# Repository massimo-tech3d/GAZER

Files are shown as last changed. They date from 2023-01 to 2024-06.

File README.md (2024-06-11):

# GAZER

it's a no-hassles, sensors based, GOTO system to drive amateurial telescopes on altazimutal mounts.

No-hassles means that you setup the scope, launch the automatic calibration procedure, acquire the GPS position on your smartphone, and you are ready to aim at your desired sky objects. **No star alignement required**. **No internet connection is required**, thus it can be used in remote, dark sky location, where data services may be unavailbale.

The telescope aim is determined via magnetometer and accelerometer sensors, while corrections/precise centering are commanded manually via a Joystick.

Note that the precision of sensors, especially magnetometers, is limited to half a degree. While this is not sufficient for precision tracking, it is well enough to hit the targeted object in the field of view of a low power eyepiece.

Object Tracking is then based on precise calculations, not on the sensors readings.

The system is composed of the following components:
* Sensors for azimuth and altitude determination. These are rigidly fixed to the telscope tube or mount.
* Arduino microcontroller (Teensy 4.0 is required) which performs
	* Magnetometer calibration
	* Sensors readings
	* Calculation of Altitude and Azimuth
	* Joystick movement readouts
* a PCB to be populated with Teensy and Stepper Drivers and to plug-in sensors and joystick cables. The PCB is finally plugged in the RPi GPIO connector.
* Raspberry Pi 3 hosts the Elixir/Nerves code to
	*  control the stepper motors
	*  read the data acquired by the Teensy microcontroller
	*  execute the astronomical algorithms for aiming and tracking objects
	*  connect to the user's smartphone to acquire GPS position
	*  provides the access point to connect the smartphone to access the **Web Based GUI** for scope control.
	*  provides a full blown version of the NGC/IC catalogues and solar system object positions
* User's Smartphone
	* The user needs to install the "GPSd Forwarder" app -- opensource and available on Google Play Store -- therefore only Android phones are currently supported, however a flutter app is in the plans which will support both Android and IOS devices. No schedule available at the moment.
	* Any mobile web browser to display the GUI

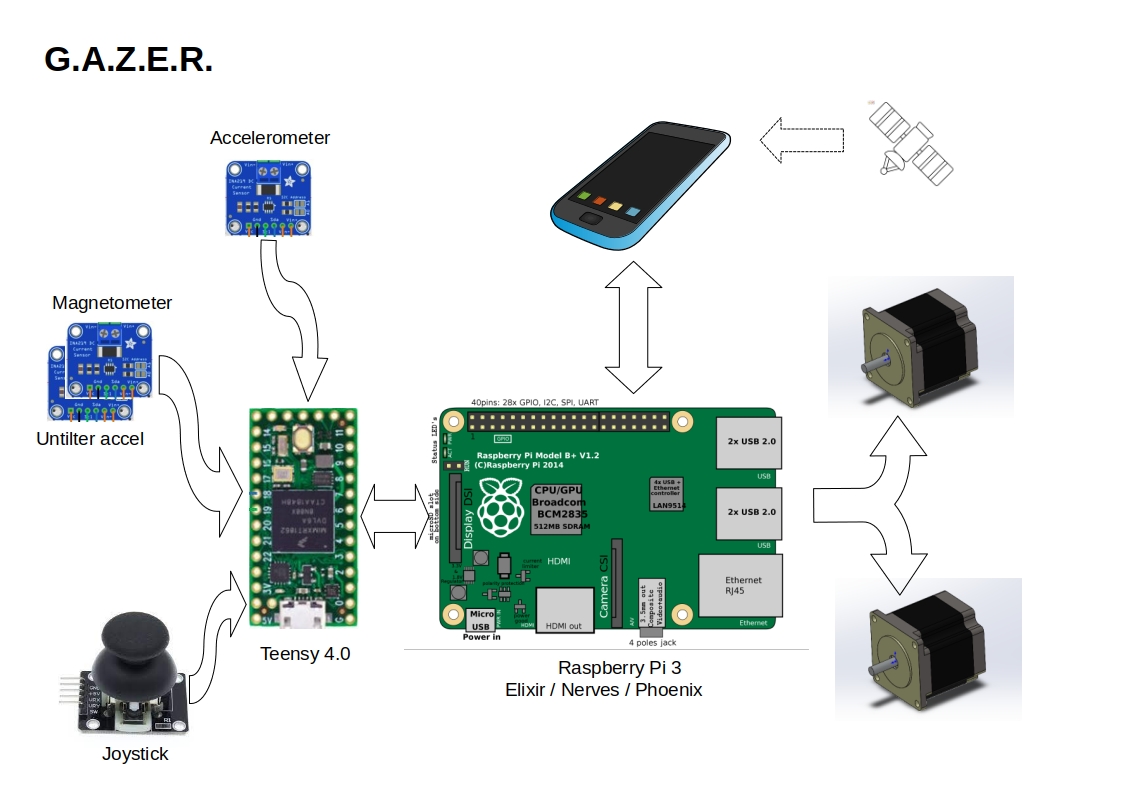
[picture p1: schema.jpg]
gazer block diagram

More information on each component is provided in the respective folders.

## What's still to be completed - work in progress

- [ ] Unit tests
- [ ] Documentation
- [ ] Flutter application as alternative to browser based GUI

## How to build
1. download gerber files from the hardware sections and get the pcb etched by your favorite service
2. follow the instructions in hardware folder
3. flash the teensy with the sketch in arduino folder
4. plug the teensy on the PCB socket
5. plug the PCB onto the RPi3 GPIO
6. flash the RPi3 card with the nerves image provided in raspberry folder. Or, if preferred, compile the source code and use the elixir/nerves commands to flash the card
7. connect sensors and motors to the RPi box
8. boot the RPi3
9. Verify the smartphone connectivity. Select gazer access point and connect to 192.168.3.1
10. install "GPSd Forwarder" from Play Store and turn it on
11. Enjoy mant star gazing nights !

## License
the project is released under AGPLv3 License (the dependencies have their own licences)

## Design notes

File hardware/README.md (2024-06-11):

## Hardware description
The Hardware for GAZER system is composed of following items:
* 1 x Raspberry Pi 3
* 1 x Teensy 4.0
* 1 x PCB - Gerber files available in this repository
* 2 x Stepper motor controller. Tested with DRV8825. Any other model with same pinout, and capable of 32 µsteps per step, should be ok
* 1 x Analogue Joystick with 5 pins connector, 2 axis 1 button
* 2 x 4 pins cables and connectors for the sensors
* 1 x 5 pins cable and connectors for the joystick
* 1 x MEMS Magnetometer. Suppeorted: LIS3MDL and PNI RM3100
* 1 x MEMS Accelerometer as untilter. Supported: MMA8451 and MPU6050
* 1 x MEMS Accelerometer for Attitude. Supported LSM6DSV

### PCB Assembly
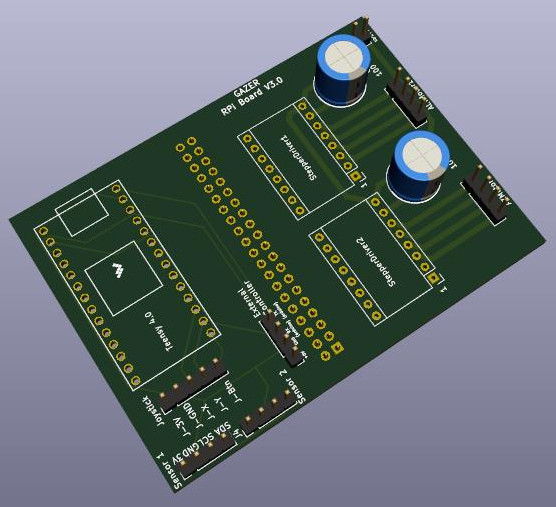
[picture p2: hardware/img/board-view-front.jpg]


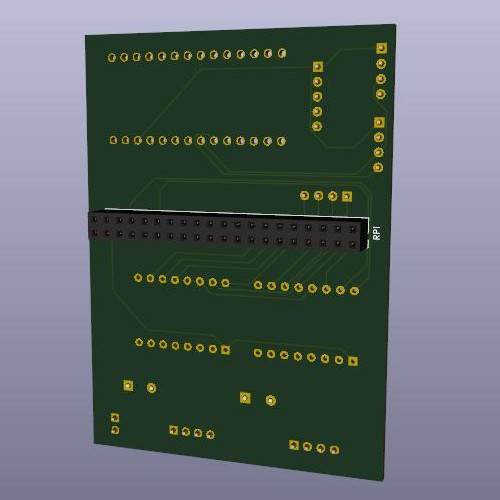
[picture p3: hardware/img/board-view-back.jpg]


The PCB shows clear indications about what needs to be plugged where. Just solder the two 100uF capacitors (beware of polarity), the sockets and pin connectors where they need to be and plug in the components.

**Note**
The 40 pin socket to the Raspberry PI needs to be positioned on the back of the PCB (solder on the front).

The two sensors sockets are interchangeable, sensors block and accelerometer can be plugged in either one.

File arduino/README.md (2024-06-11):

The repository includes two sketches, Gazza2D and Gazza3D.

Their role is to read the sensors and calculate Altitude and Azimuth of the Telescope OTA for the main Gazer app, which run on the connected Raspberry Pi 3.

The sensors required are an accelerometer (rotating with the OTA) to calculate the Altidude, and a Magnetometer to calculate the Azimuth.

The difference between the two sketches is how the magnetometer is handled.

# 2D
The 2D Sketch requires the magnetometer to be positioned flat on the mount and rotate with it, disregarding the OTA inclinations. It uses a second accelerometer on the same board of the magnetometer to compensate for potential off levels - tripod and mount or a mismounted magnetometer board, **Small degrees off level (say up to 5° or 10° at best) can be compensated by the second accelerometer**

The second accelerometer is strongly reccommended but the system will work also without it. In this case you should ensure that the telescope mount and the magnetometer itself are perfectly level, or the Azimuth readings will be way off.

The sensor calibration carousels 360° back and forth the azimuth axis, with the OTA conveniently positioned verticallly, and then performs 2D ellipse fitting of the sensors readings to calculate hard iron and soft iron correction parameters.

The carouselling requires approximately 4 minutes.

# 3D
The 3D Sketch requires magnetometer and accelerometer on the same board on the OTA rotating with the OTA both in Azimuth and Altitude. The second accelerometer in not required.

The sensor calibration carousels 360° back and forth two times the azimuth axis, with the OTA positioned at 0° (horizontal), 45°, 90° and 135° (backtilted), and then performs 3D ellipsoid fitting of the sensors readings to calculate hard iron and soft iron correction parameters.

The carouselling requires approximately 10 minutes.

## Which should be chosen
It depends on you mount and setup. For dobsons you should chose the 2D version, since it does not backtilt the OTA and because there will not be problems in finding a good place to install the magnetomer board, away at least 20cm from motors, The aluminium/wooden OTA will not cause interferences.

It also takes less time to calibrate.

Telescopes mounted on other types of platform can also use the 2D skecth, if you can position the magnetometer away from motors and away from the OTA (if this is made of ferromagnetic metal).

If this is not the case, it is necessary to use the 3D version and hook the sensors on the OTA (if not ferromagnetic) or in a spot on the mount that follows the OTA movements.

In case of 2D version and magnetometer too close to metallic OTA, this will disturb the magnetic field when changing it's altitude. There is a compensation function to limit this phenomenon but it is reccommended to avoid it at all, rather than compensating it.

In synthesis the main advantages of the two setups are:
* 2D version
	- faster calibration procedure
	- OTA vertical during carouselling - no issues with space requirements
	- does not backtilt the OTA during calibration
* 3D version
	- less number of sensors
	- just one sensor board and one sensor cable

In both sketches the magnetometer calibration procedure is intiated by the user and coordinated by the Elixir software on the Raspberry.

The Accelerometer calibration is much simpler, the OTA is placed horizontal and a reading is taken via a button on the phone GUI. The same is then repeatd with the OTA in vertical position.

# Hardware parts

## Microcontroller
The magnetometer calibration and untilting require extensive float operations. Therefore the AVR Microcontrollers are not suitable. The reccommended choice is a Teensy 4.0 board.

We have briefly tested the skecth also on an ESP32 WROOM board and it compiles and runs, however we have not done any extensive testing. We preferred the Teensy over the ESP32 because of its smaller footprint.

The sketch, and the PCB, only support the Teensy 4.0. Support for the ESP, as well as other same level micros, would require changing the pinout mappings in the sketch and changing the PCB design.

## Supported MEMS are:
3D version:
* Magnetometers: ST LIS3MDL (reccommended), PNI RM3100
* Accelerometer: ST LSM6DSV (reccommended), InvenSense MPU6050

2D version:
* Magnetometers: ST LIS3MDL (reccommended), PNI RM3100
* Accelerometer: ST LSM6DSV (reccommended), NXP MMA8451
* Untilt accelerometers: NXP MMA8451 (reccommended), InvenSense MPU6050

Note: the two accelerometers must be different. Not possible to use MMA8451 in both positions.

Datasheets:
* ST LIS3MDL https://www.st.com/resource/en/datasheet/lis3mdl.pdf
* ST LSM6DSV https://www.st.com/resource/en/datasheet/lsm6dsv.pdf
* PNI RM3100 https://www.tri-m.com/products/pni/RM3100-User-Manual.pdf
* NXP MMA8451 https://www.nxp.com/docs/en/data-sheet/MMA8451Q.pdf
* IS MPU6050 https://invensense.tdk.com/wp-content/uploads/2015/02/MPU-6000-Datasheet1.pdf

other sensors, supporting i2c interface, can be employed by writing the relevant (simple) header file

The usual breakout boards vendors will have BBs for all these sensors. Exception is the RM3100 whose BB is sold directly on the PNI site. Keep away from the chinese ones sold on Amazon and labelled "Military grade", they are poor quality and do not support i2c interface. During the development, the PNI BB was not available and we had to use an SPI to i2c converter, which complicated a lot the Sensor Block hardware.

For this reason the RM3100 is not the reccommended choice otherwise it might be, because the sensor is by far the less noisy of the lot. If you can access the PNI BB, that could be a very good choice (though we haven't tested it).

## Joystick
any analog joystick for arduino with 5 contacts will fit. Just needs X and Y movements and pushbutton function. Wiring is explained in the hardware section of this repository.

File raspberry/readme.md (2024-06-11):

# installation instructions

flash the firmware.x.y.fw file to a microsd card and plug it in the Raspberry Pi3

(firmware.fw sha256: 3307be91864f4990a0d53673387666f02c0a14a20f214d5dde0356f2f8def148

 on Ubuntu it can be checked with the command **sha256sum firmware.x.y.fw** if the file is ok you should get the number above)

If you prefer to compile from source code:
* Ensure elixir is up to date (1.13) and run *mix install nerves* (see https://nerves-project.org/)
* Enter both the ui and firmware directories and execute "mix deps.get"
* execute
	* *export MIX_TARGET=rpi3*
	* *export MIX_ENV=prod*
	* *mix firmware*
	* *mix burn* to flash the resulting firmware.fw file to a microsd card. Then plug it in the Raspberry Pi3
* if you have already flashed the firmware once, you can reflash by simply connecting the RPi to the lan and executing *mix upload nerves.local* from the firmware directory.

## 	post installation instructions
When booted the Raspberry will provide it's own access point, gazer, to which the smartphone can connect.

If the browser doesn't open GAZER home page automatically, it can be reached by visiting the address 192.168.3.1 with any browser after half a minute or so.

From the same smartphone launch the app "GPSd Forwarder" (available on Play Store and github), wait for GPS acquisition and activate the data forwarding to 192.168.3.1:1111

The app can be switched off as soon as the GAZER home page shows correct coordinates and time.

After everything is connected, and GPS position is reflected in the webapp, the calibrations should be performed.

Tap on the Calibration tab, read the instructions and proceed in the order suggested.

Now you can search for celestial objects to observe using one of the three widgets provided:

#### Find Solar System Object
to find the Moon and the 8 planets (Pluto included) by name
#### Filter DSO
by specifying the main characteristics (Magnitude, type of object etc.) of the object desired, a list of compatible objects will be provided for you to choose.
Objects lower than 15° from the horizon are considered not visible and will not be shown.
#### Find DSO
the full NGC and IC catalogues are included. For example NGC 1976 or M 42 will take you straight to the Orion Nebula.
#### Find Double Star
this has not been developed yet

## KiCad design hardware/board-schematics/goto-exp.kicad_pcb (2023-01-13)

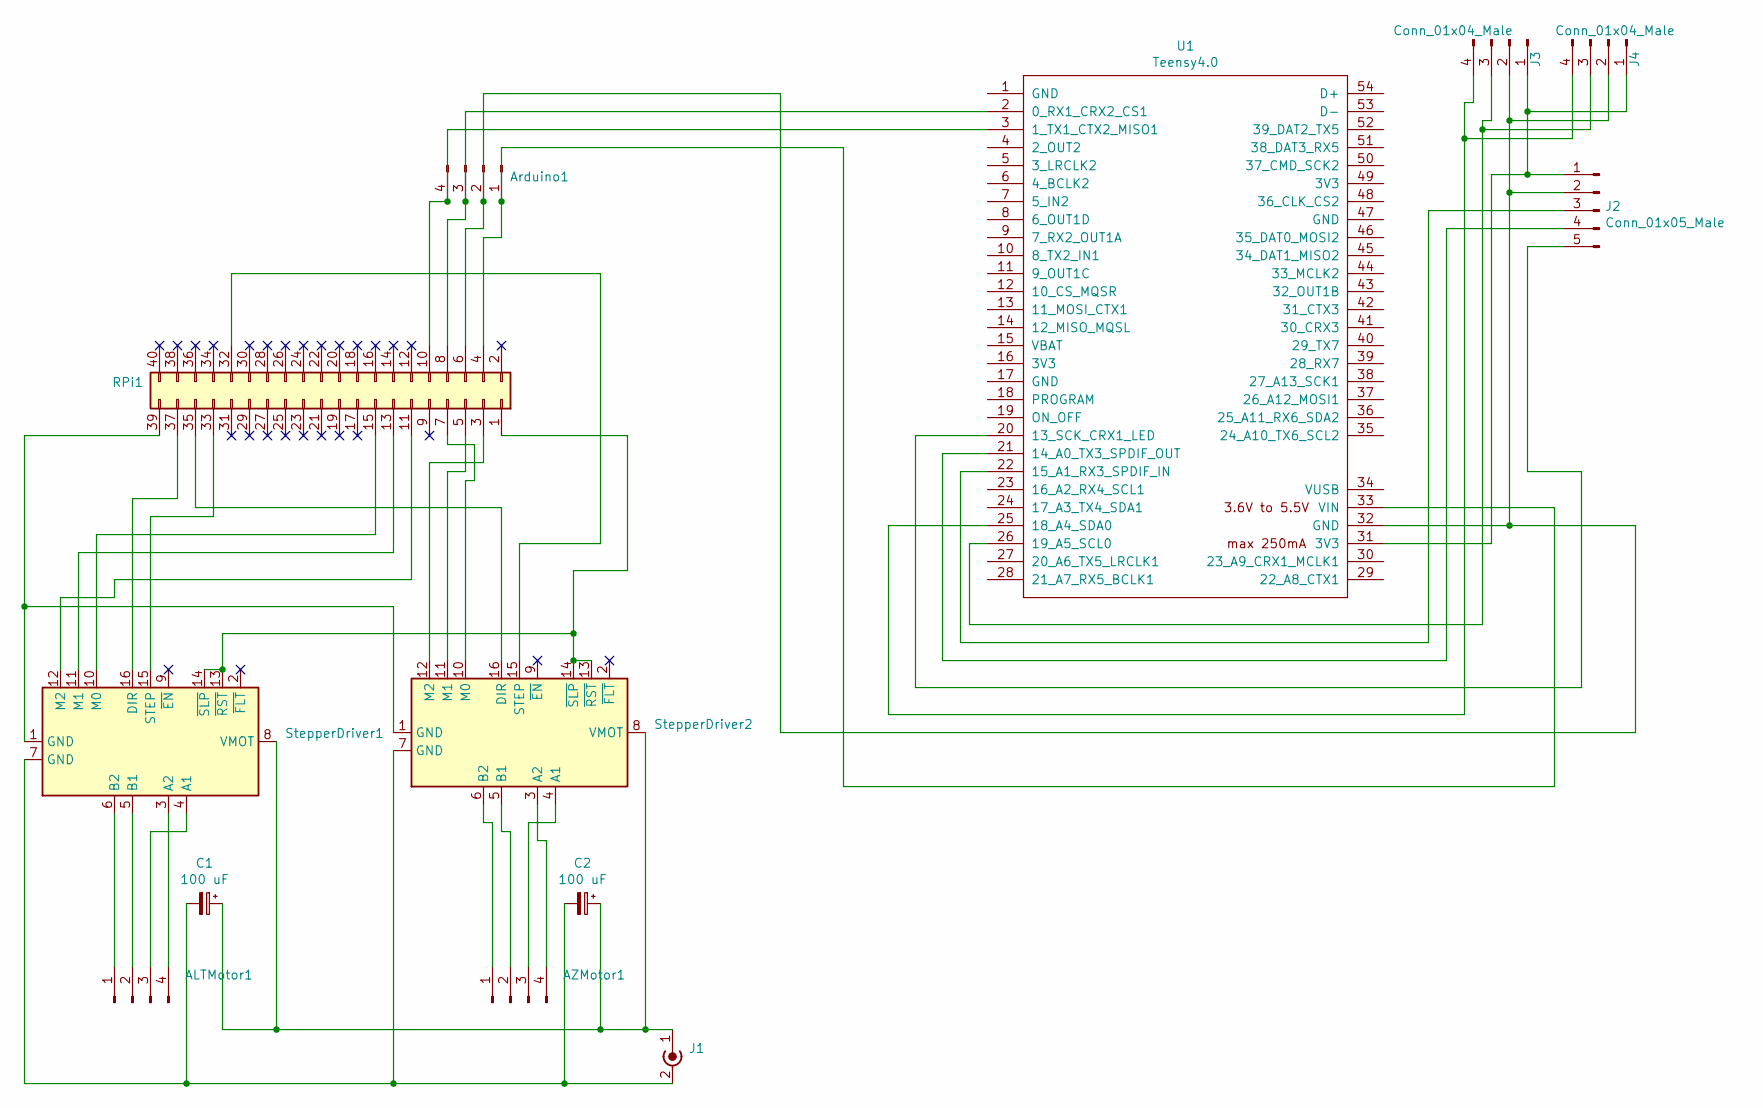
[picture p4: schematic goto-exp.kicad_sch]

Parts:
ALTMotor1: Conn_01x04_Male; PinHeader_1x04_P2.54mm_Vertical
AZMotor1: Conn_01x04_Male; PinHeader_1x04_P2.54mm_Vertical
Arduino1: Conn_01x04_Male; PinHeader_1x04_P2.54mm_Vertical
C1, C2: 100 uF; CP_Radial_D10.0mm_P5.00mm
J1: Conn_Coaxial_Power; PinHeader_1x02_P2.54mm_Vertical
J2: Conn_01x05_Male; PinHeader_1x05_P2.54mm_Vertical
J3, J4: Conn_01x04_Male; PinHeader_1x04_P2.54mm_Vertical
RPi1: Conn_02x20; PinSocket_2x20_P2.54mm_Vertical
StepperDriver1, StepperDriver2: Pololu_Breakout_DRV8825; Pololu_Breakout-16_15.2x20.3mm
U1: Teensy4.0; Teensy40

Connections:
unnamed: ALTMotor1.1, StepperDriver1.6 (B2)
unnamed: ALTMotor1.2, StepperDriver1.5 (B1)
unnamed: ALTMotor1.3, StepperDriver1.4 (A1)
unnamed: ALTMotor1.4, StepperDriver1.3 (A2)
unnamed: AZMotor1.1, StepperDriver2.6 (B2)
unnamed: AZMotor1.2, StepperDriver2.5 (B1)
unnamed: AZMotor1.3, StepperDriver2.4 (A1)
unnamed: AZMotor1.4, StepperDriver2.3 (A2)
unnamed 8: Arduino1.1, RPi1.4, U1.33 (VIN); also elsewhere on the board
unnamed 9: Arduino1.2, J2.2, J3.2, J4.2, RPi1.6, U1.32 (GND); also elsewhere on the board
unnamed 10: Arduino1.3, RPi1.8, U1.2 (0_RX1_CRX2_CS1); also elsewhere on the board
unnamed 11: Arduino1.4, RPi1.10, U1.3 (1_TX1_CTX2_MISO1); also elsewhere on the board
unnamed: C1.1, C2.1, J1.1 (In), StepperDriver1.8 (VMOT), StepperDriver2.8 (VMOT)
unnamed: C1.2, C2.2, J1.2 (Ext), StepperDriver1.7 (GND), StepperDriver2.7 (GND)
unnamed: J2.1, J3.1, J4.1, U1.31 (3V3)
unnamed: J2.3, U1.22 (15_A1_RX3_SPDIF_IN)
unnamed: J2.4, U1.21 (14_A0_TX3_SPDIF_OUT)
unnamed: J2.5, U1.20 (13_SCK_CRX1_LED)
unnamed: J3.3, J4.3, U1.26 (19_A5_SCL0)
unnamed: J3.4, J4.4, U1.25 (18_A4_SDA0)
unnamed 20: RPi1.1, StepperDriver1.13 (~RST), StepperDriver1.14 (~SLP), StepperDriver2.13 (~RST), StepperDriver2.14 (~SLP); also elsewhere on the board
unnamed 22: RPi1.3, StepperDriver2.12 (M2); also elsewhere on the board
unnamed 23: RPi1.5, StepperDriver2.11 (M1); also elsewhere on the board
unnamed 24: RPi1.7, StepperDriver2.10 (M0); also elsewhere on the board
unnamed 26: RPi1.11, StepperDriver1.12 (M2); also elsewhere on the board
unnamed 28: RPi1.13, StepperDriver1.11 (M1); also elsewhere on the board
unnamed 30: RPi1.15, StepperDriver1.10 (M0); also elsewhere on the board
unnamed 47: RPi1.32, StepperDriver2.15 (STEP); also elsewhere on the board
unnamed 48: RPi1.33, StepperDriver1.15 (STEP); also elsewhere on the board
unnamed 50: RPi1.35, StepperDriver2.16 (DIR); also elsewhere on the board
unnamed 52: RPi1.37, StepperDriver1.16 (DIR); also elsewhere on the board
unnamed 54: RPi1.39, StepperDriver1.1 (GND), StepperDriver2.1 (GND); also elsewhere on the board

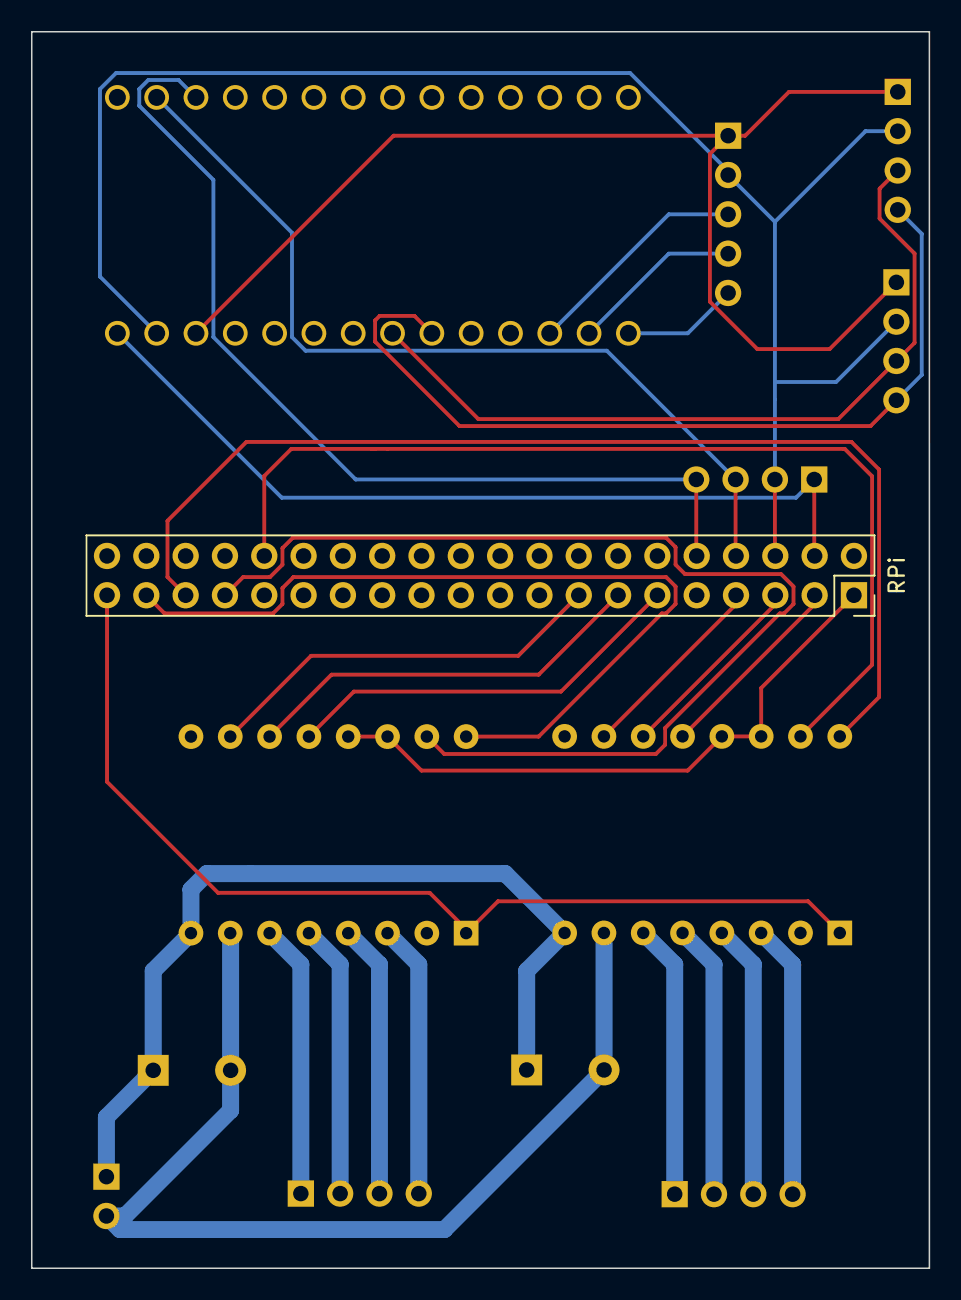
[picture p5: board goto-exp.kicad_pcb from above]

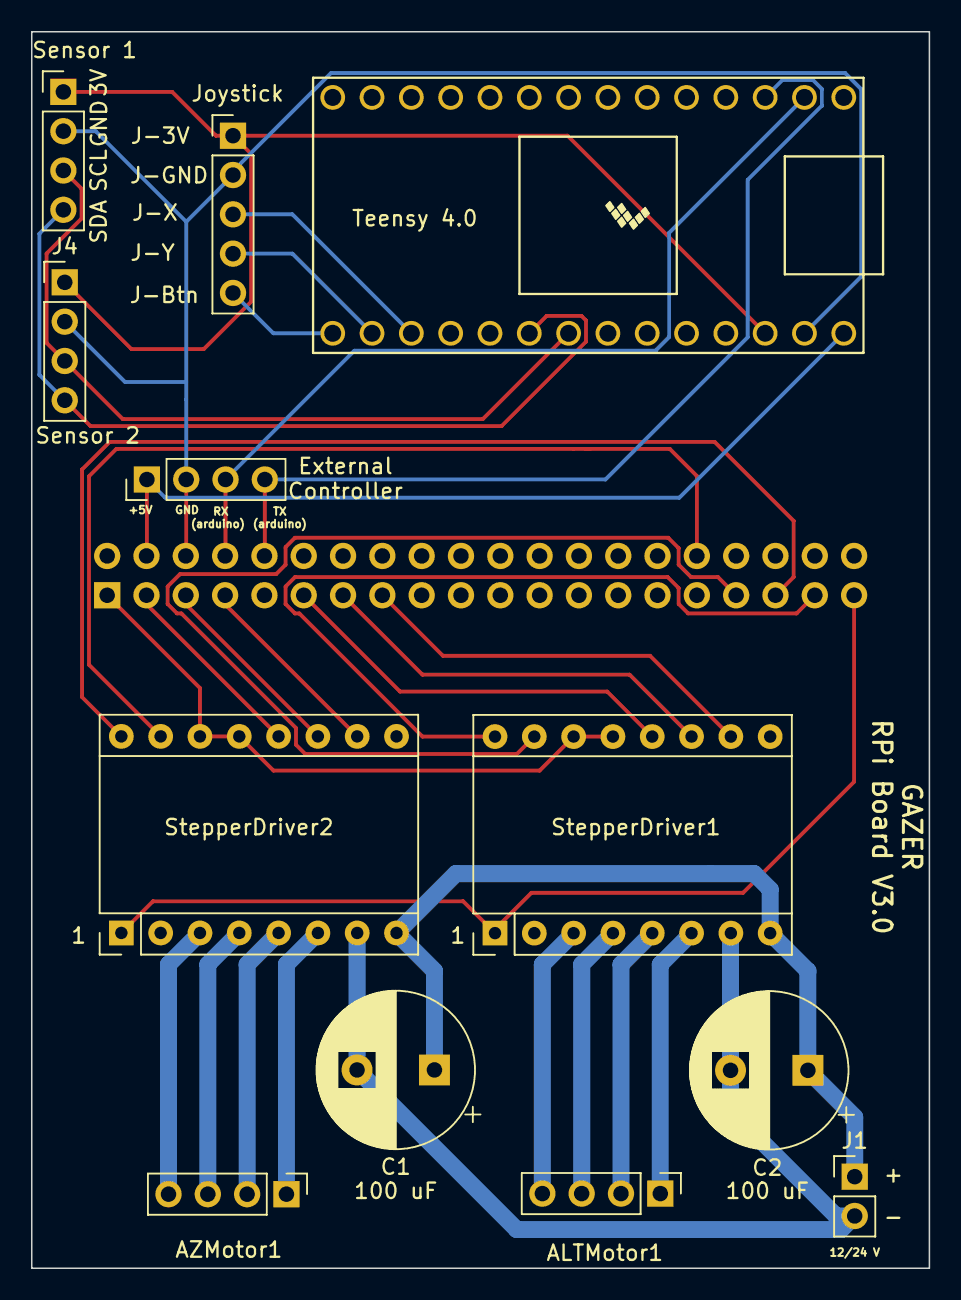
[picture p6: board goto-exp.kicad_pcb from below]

Board: 2 copper layers, 58.0 x 79.9 mm, 13 parts (12 on the bottom side), 32 nets.

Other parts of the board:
RPi: Conn_02x20; PinSocket_2x20_P2.54mm_Vertical

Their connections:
unnamed 8: RPi.4; also elsewhere on the board
unnamed 9: RPi.6; also elsewhere on the board
unnamed 10: RPi.8; also elsewhere on the board
unnamed 11: RPi.10; also elsewhere on the board
unnamed 20: RPi.1; also elsewhere on the board
unnamed 22: RPi.3; also elsewhere on the board
unnamed 23: RPi.5; also elsewhere on the board
unnamed 24: RPi.7; also elsewhere on the board
unnamed 26: RPi.11; also elsewhere on the board
unnamed 28: RPi.13; also elsewhere on the board
unnamed 30: RPi.15; also elsewhere on the board
unnamed 47: RPi.32; also elsewhere on the board
unnamed 48: RPi.33; also elsewhere on the board
unnamed 50: RPi.35; also elsewhere on the board
unnamed 52: RPi.37; also elsewhere on the board
unnamed 54: RPi.39; also elsewhere on the board

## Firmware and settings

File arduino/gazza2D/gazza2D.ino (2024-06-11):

/**************************************************************************************
 * This is the final version of gazza. refactored to isolate the sensors
 * initialization and reading functions in semsors.h file. The sensors() function call
 * tries to initialize separatetly mag and the two accel sensors.
 * 
 * Sensors initialization parameters are defined in the respective header files in the sensors
 * subdirectory
 * 
 * The sensors supported are:
 * - MAGNETOMETERS: ST LIS3MDL, PNI RM3100 (only chinese breakout board, not reccommended, get a PNI BB instead and use it's i2c interface)
 * - ACCELEROMETERS: ST LSM6DSV for Altitude detection. For untilt either NXP MMA8451 or InvenSense MPU6050 (but this is very noisy)
 * 
 * Serial1 IO is to/from the Raspberry
 * Serial  IO is to/from the optional usb cable, typically used for testing purposes
 * 
 * Created by Massimo Tasso, January, 1, 2023 except where otherwise stated.
 * Released under GPLv3 License - see LICENSE file for details.
 **************************************************************************************/

#include "sensors.h"
#include "joystick.h"
#include "compass.h"
#include "m_calibration.h"
#include "m_compensation.h"
#include "a_calibration.h"
#include "defines.h"

unsigned long magLoopIntervalMs;
unsigned long untiltLoopIntervalMs;
unsigned long accelLoopIntervalMs;
unsigned long magCalLoopIntervalMs;
unsigned long magCompLoopIntervalMS = 100;
unsigned long headingLoopIntervalMs;
const unsigned long outputLoopIntervalMs = 100;  // sensors sent to Raspberry at 10 Hz - sounds enough
const unsigned long devoutputLoopIntervalMs = 200;  // outputs mag and untiltacc raw data - temporary, can be removed after development tests

unsigned long last_mag_time = millis();
unsigned long last_untilt_time = millis();
unsigned long last_accel_time = millis();
unsigned long last_mag_cal_time = millis();
unsigned long last_compensation_time = millis();
unsigned long last_heading_time = millis();
unsigned long last_print_time = millis();

bool m_calib_on = false;        // true if calibration data collection is in progress
bool m_calib_complete = false;

bool compensation_on = false;        // true if compensation data collection is in progress
bool compensation_complete = false;
float compensation_reference = 180.0;

uint8_t debug;

// Buffer for holding general text output
#define MAX_LEN_OUT_BUF 130
char output_str[MAX_LEN_OUT_BUF];

/*
 * Latest orientation data
 * magnetometer values are kalman smoothed, calibrated and untilted
 * accelerometer values are kalman smoothed
 */
float azimuth = 0;
// float azimuth_ALT = 0;
float altitude = 0;
float acc[3];
float mag[3];
float unt_acc[3];

void setup() {
  // put your setup code here, to run once:
  Serial.begin(115200);   // Serial: Console
  Serial1.begin(115200);  // Serial1: raspberry
  while(!Serial1) {
    delay(1);
  }

  initJoystick();
  Serial.println("STARTING");
  /* Initialise the sensors */
  while(!(sensors())) {
    Serial.println("Sensor error");
    Serial1.println("Sensor error");
    delay(1000);
  }

  // need to initialize the values here because they depend on sensors() result
  magLoopIntervalMs = 1000 / MAG_DATARATE;
  untiltLoopIntervalMs = 1000 / UNTILTER_DATARATE;  // 2;  // 500 Hz;
  accelLoopIntervalMs = 1000 / ACCEL_DATARATE;
  headingLoopIntervalMs = max(magLoopIntervalMs, accelLoopIntervalMs);  // used only if heading is kalman smoothed -- to be decided
  
  Serial.print("MAG Datarate: ");Serial.println(MAG_DATARATE);
  Serial.print("ACC Datarate: ");Serial.println(ACCEL_DATARATE);
  Serial.print("UNT Datarate: ");Serial.println(UNTILTER_DATARATE);
  Serial.print("MAG interval ms: ");Serial.println(magLoopIntervalMs);
  Serial.print("UNTILT interval ms: ");Serial.println(untiltLoopIntervalMs);
  Serial.print("ACC interval ms: ");Serial.println(accelLoopIntervalMs);
}

void checkSerial();
void checkSerial1();

/**
 * main cycle.
 * actions to perform, with different intervals
 * 
 * - accelererometer readings - accelLoopIntervalMS
 * - untilt accelerometer readings - 500 Hz, 2ms
 * - magnetometer readings - magLoopIntervalMS
 * - samples acquisition for magnetometer calibration - interval calculated basing on rotation time and number of samples
 * - samples acquisition for magnetometer compensation (mag data and accel data)
 * - ALT-AZ computation
 * - ALT-AZ sendout to raspberry (and serial console)
 **/
void loop() {
    unsigned long timestamp = millis();
    // ALTITUDE ACC
    if ((timestamp - last_accel_time) >= accelLoopIntervalMs) {                       // time to read accelerometer
        last_accel_time = timestamp;
        accel_readings(acc, debug);
        a_calibrate(acc);                                                             // call a_calibrate even if calibration is not done, won't harm
    }

    // UNTILT ACC
    if ((timestamp - last_untilt_time) >= untiltLoopIntervalMs) {                     // time to read untilt accelerometer
        last_untilt_time = timestamp;
//        Serial.println("LOOP Reading untilter");
        get_untilt_raw(unt_acc, debug);
//        Serial.print("LOOP untilter READ ");Serial.print(unt_acc[0]);Serial.print(" ");Serial.print(unt_acc[1]);Serial.print(" ");Serial.println(unt_acc[2]);
    }

    // MAGNETOMETER
    if ((timestamp - last_mag_time) >= magLoopIntervalMs) {                           // time to read magnetometer
        last_mag_time = timestamp;
        mag_readings(mag, debug);
        if (m_calib_on && (timestamp - last_mag_cal_time) >= magCalLoopIntervalMs) {        // time to read mag calibration sample
            last_mag_cal_time = timestamp;
    
            float unt_acc[3];
            get_untilt_raw(unt_acc, debug);
    
            int to_go = add_sample(mag, unt_acc, debug);
            if(!to_go) {
                m_calib_on = false;
                m_calib_complete = true;
                Serial.print("AZ_CORR ");Serial.println(AZ_CORR*RadToDeg);
                Serial.println("M_CAL, points collected");
                Serial1.println("M_CAL, points collected");  // tell Raspberry that magnetometer calibration is completed
            } else {
                Serial.print(millis());Serial.print(" \tM Calibration togo ");Serial.println(to_go);
            }
        }
        m_calibrate(mag, unt_acc, debug);                    // can call m_calibrate even if calibration is not completed, won't harm
    }

    // MAGNETOMETER COMPENSATION
    if (compensation_on && (timestamp - last_compensation_time) >= magCompLoopIntervalMS) {  // time to read mag compensation sample
        last_compensation_time = timestamp;
        int to_go = add_compensation_sample(compensation_reference, altitude, azimuth, debug);
        if(!to_go) {
          compensation_on = false;
          compensation_complete = true;
          Serial.println("M_COMP, compensation map completed");
          Serial1.println("M_COMP, compensation map completed");  // tell Raspberry that magnetometer compensation is completed
        } else {
          Serial.print(millis());Serial.print(" \tM Compensation togo ");Serial.println(to_go);
        }
    }

    // AZIMUTH
    if ((timestamp - last_heading_time) >= headingLoopIntervalMs) {       // time to calculate ALT/AZ using most recent readings
        last_heading_time = timestamp;
//        altitude = elevation(acc[0], acc[2], debug);
        altitude = elevation(acc, debug);
//        azimuth = flatCompass(unt_acc, mag, debug);
        azimuth = compass3D(unt_acc, mag, debug);
        // azimuth_ALT = flatCompassALT(unt_acc, mag, debug);
    }

    // OUTPUTS
    if ((timestamp - last_print_time) >= outputLoopIntervalMs) {          // time to send to serial ALT/AZ
        last_print_time = timestamp;
        snprintf(output_str, MAX_LEN_OUT_BUF, "SENSORS, AZ, %+3.3f, ALT, %+3.3f,", azimuth, altitude);
        if(!m_calib_on) {
            if((uint8_t)(debug | ~DEBUG_UNTILT_ACC)==255) {
                Serial.print("UNT ");Serial.print(unt_acc[0], 4);Serial.print(" ");Serial.print(unt_acc[1], 4);Serial.print(" ");Serial.print(unt_acc[2], 4);
                Serial.print(" ");Serial.print(mag[0], 4);Serial.print(" ");Serial.print(mag[1], 4);Serial.print(" ");Serial.println(mag[2], 4);
            }
            if(!debug){  // don't print if debug is active (!= 0)
                Serial.println(output_str);
                // Serial.print("Alternative AZ ");Serial.println(azimuth_ALT);
            }
        }
        Serial1.println(output_str); // send to Raspberry
    }

    checkSerial();        // manual commands
    checkSerial1();       // commands from raspberry
    checkJoystick(debug);
}


/*
 * calibration command must be paired with the duration to execute one full round and back
 * to be parsed, e.g.:
 * 
 *    calibstart 300
 * 
 * will split SAMPLES (1000, or change in calibration.h) readings over 300 seconds.
 * The Telescope controlled by the Raspberry must be able to complete the required movements
 * in the specified time
 */

void debug_on(String msg);
void debug_off(String msg);
void start_mag_calibration(String msg);
void start_mag_compensation(String msg);
void parse_acc_calibration(String msg);

void processCommand(String command) {
  Serial.println(command);
  if(command.startsWith("m_calibration")) {
    if(!m_calib_complete) {
      start_mag_calibration(command);
    }
  } else if(command.startsWith("m_compensation")) {
    start_mag_compensation(command);
  } else if(command=="untilt_zero") {
    zero_untilt();
  } else if(command=="cal_type") {
    Serial1.println("2D");
  } else if(command.startsWith("B_mag")) {
    set_bmag(command);
  } else if(command=="block_v") {
    sensor_block_vertical = true;
  } else if(command=="block_h") {
    sensor_block_vertical = false;
  } else if(command=="print_compensation") {
    print_compensation_values();
  } else if(command=="a_calibration_h") {
    read_horizontal_accel();
  } else if(command=="a_calibration_v") {
    read_vertical_accel();
  } else if(command.startsWith("set_a_calibration")) {
    parse_acc_calibration(command);
  } else if(command=="export_a_calibration") {
    export_a_calibration();
  } else if(command=="print_a_cal") {
    print_a_cal();
  } else if(command=="analysis_carousel") {
    print_carousel_data();
  } else if(command=="samples") {
    SendSamples();
  } else if(command=="ellipse") {
    SendEllipse();    
  } else if(command=="show_m_cal") {
    printIrons();
  } else if(command.startsWith("debug")) {  // valid debugs: MAG_CAL, MAG_RAW, UNTILT, ALT_ACC, ALTAZ, JOYSTICK, ALL
    debug_on(command);
  } else if(command.startsWith("nodebug")) {
    debug_off(command);
  } else {
    Serial.println(command);Serial.println("To Serial: UNRECOGNIZED COMMAND");
    Serial1.print("To Serial1: UNRECOGNIZED COMMAND ");Serial.println(command);
  }
}

// RECEIVES COMMANDS FROM CONSOLE - used during develoment and testing
// Tipically commands to start calibrations or to turn on/off debugging
void checkSerial(){
  if(!Serial.available()){
    return;
  } else {
    String command = Serial.readStringUntil('\n');
    processCommand(command);
  }
}

// RECEIVES COMMANDS FROM RASPBERRY
// Tipically commands to start calibrations
void checkSerial1(){
  if(!Serial1.available()){
    return;
  } else {
    String command = Serial1.readStringUntil('\n');
    processCommand(command);
  }
}

void debug_on(String msg) {
    String values = msg.substring(6, msg.length());    // extract second word, which is values to turn debugging on, from command string
    if(values == "mag_raw")
        debug |= DEBUG_MAG_RAW;
    if(values == "mag_cal")
        debug |= DEBUG_MAG_CAL;
    if(values == "untilt")
        debug |= DEBUG_UNTILT_ACC;
    if(values == "alt_acc")
        debug |= DEBUG_ALT_ACC;
    if(values == "alt")
        debug |= DEBUG_ALT;
    if(values == "az")
        debug |= DEBUG_AZ;
    if(values == "joystick")
        debug |= DEBUG_JOYSTICK;
    if(values == "all")
        debug = 255;
    Serial.print("Debug: ");Serial.println(debug);
}

void debug_off(String msg) {
    String values = msg.substring(8, msg.length());    // extract second word, which is values to turn debugging on, from command string
    if(values == "mag_raw")
        debug &= ~DEBUG_MAG_RAW;
    if(values == "mag_cal")
        debug &= ~DEBUG_MAG_CAL;
    if(values == "untilt")
        debug &= ~DEBUG_UNTILT_ACC;
    if(values == "alt_acc")
        debug &= ~DEBUG_ALT_ACC;
    if(values == "alt")
        debug &= ~DEBUG_ALT;
    if(values == "az")
        debug &= ~DEBUG_AZ;
    if(values == "joystick")
        debug &= ~DEBUG_JOYSTICK;
    if(values == "all")
        debug = 0;
    Serial.print("Debug: ");Serial.println(debug);  
}

void start_mag_calibration(String msg) {
  m_calib_on = true;
  // NOTE: substring below from X, where X is the length (base 1) of the 1st word of command: m_calibration
  String seconds = msg.substring(13, msg.length());    // extract second word, which is duration in seconds, from command string
  int duration_in_seconds = seconds.toInt();
  magCalLoopIntervalMs = init_cal(duration_in_seconds * 1000); // result in milliseconds for 1000 calibration readings
}

void start_mag_compensation(String msg) {
  compensation_on = true;
  Serial.print("Seconds: ");
  String seconds = msg.substring(15, msg.length());    // extract second word, which is duration in seconds, from command string
  int duration_in_seconds = seconds.toInt();
  Serial.println(duration_in_seconds);
  /***** TODO BAD CALCULATIONS *****/
  magCompLoopIntervalMS = init_compensation(duration_in_seconds * 1000); // result in milliseconds for 1000 calibration readings
  Serial.print("Interval: ");
  Serial.println(magCompLoopIntervalMS);
  compensation_reference = azimuth;
  Serial.print("Comp Reference: ");Serial.println(azimuth);
}

/*
 * Receives from Raspberry the last accel calibration saved
 * parses it and saves it making it unnecessary to calibrate
 * again the accelerometer.
 */
void parse_acc_calibration(String msg) {
  float ox = 0;
  float oz = 0;
  float gx = 1;
  float gz = 1;
  int ParCount = 0;
  String pars[4];
  String a_cal_pars = msg.substring(18, msg.length());
  while(ParCount < 4){
    int idx = a_cal_pars.indexOf(',');
    if(idx == -1) {
      pars[ParCount] = a_cal_pars;
      break;
    } else {
      pars[ParCount++] = a_cal_pars.substring(0, idx);
      a_cal_pars = a_cal_pars.substring(idx+1);
    }
  }
  ox = pars[0].toFloat();
  gx = pars[1].toFloat();
  oz = pars[2].toFloat();
  gz = pars[3].toFloat();
  Serial.print("OX: ");Serial.print(ox);Serial.print("\tGX: ");Serial.print(gx);Serial.print("\tOZ: ");Serial.print(oz);Serial.print("\tGZ: ");Serial.println(gz);
  set_a_calibration(ox, gx, oz, gz);
  Serial.println("Acc calibration saved");
}

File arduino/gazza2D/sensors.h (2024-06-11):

/******
 * Sensors initialization and readings
 *   abstracted functions
 *   can handle either two separate sensors or a combined magnetometer/accelerator sensor
 * 
 * Created by Massimo Tasso, January, 1, 2023
 * Released under GPLv3 License - see LICENSE file for details.
 ******/
 
#include "sensors/LIS3MDL.h"
#include "sensors/RM3100.h"
#include "sensors/MMA8451.h"
#include "sensors/LSM6DSV.h"
#include "sensors/MPU6050.h"
#include "defines.h"
#include <Wire.h>
#include <SimpleKalmanFilter.h>

/*
 * Untilted MAG is a magnetometer sensor combined with an accelerometer/gyro to compensate for non complanarity with the horizontal plane
 */
bool LIS3MDL_MAG = false;
bool RM3100_MAG = false;
bool MMA_ACCEL = false;
bool LSM_ACCEL = false;
bool MPU6050_ACCEL = false;
bool MMA_UNTILTER = false;
bool MPU6050_UNTILTER = false;

int ACCEL_DATARATE = 0;
int MAG_DATARATE = 0;
int UNTILTER_DATARATE = 0;
bool untilter = false;
double aRMS;

bool sensor_block_vertical = false;

float B = 46.8;  // magnitude of earth mag vector - to be received from raspberry

// the untilting functions require as smooth as possible accelerometer readings
SimpleKalmanFilter* kf_untilt_x;
SimpleKalmanFilter* kf_untilt_y;
SimpleKalmanFilter* kf_untilt_z;
SimpleKalmanFilter* kf_mag_x;
SimpleKalmanFilter* kf_mag_y;
SimpleKalmanFilter* kf_mag_z;
SimpleKalmanFilter* kf_acc_x;
SimpleKalmanFilter* kf_acc_y;
SimpleKalmanFilter* kf_acc_z;

bool mag_smooth = false;
bool acc_smooth = false;
bool untilt_smooth = false;


/*
// Kalman filters parameters - defined in magnetometer modules
float K_ERR_AZ = 0.01;  // default value - meaning: 
float K_Q_AZ = 1.5;     // default value - meaning: how much we expect the measurement to vary. Quite small, fastest rotation at 3°/sec when calibrating. Generally below 1"/sec
// Kalman filters parameters - defined in accelerometer modules
float K_ERR_ALT = 0.01;  // default value
float K_Q_ALT = 0.5;     // default value - meaning: how much we expect the measurement to vary. Even smaller than azimuth, the scope rotates at 1°/sec when slewing. Generally below 1"/sec
*/

void zero_untilt();

void findUntilter() {
    float K_ERR_UNTILT;
    float K_Q_UNTILT;
    if((!MMA_ACCEL) & (init_accelerometer_MMA())) {
        Serial.println("MMA8451 Untilter Accelerometer Found");
        untilter = true;
        MMA_UNTILTER = true;
        UNTILTER_DATARATE = ACCEL_DATARATE_MMA;
        K_ERR_UNTILT = K_ERR_MMA;
        K_Q_UNTILT = K_Q_MMA;
        untilt_smooth = true;  // MMA8451 is best if smoothed
    } else if(init_accelerometer_MPU6050()) {
        Serial.println("MPU6050 Untilter Accelerometer Found");
        untilter = true;
        MPU6050_UNTILTER = true;
        UNTILTER_DATARATE = ACCEL_DATARATE_MPU6050;
        K_ERR_UNTILT = K_ERR_MPU_FAST;
        K_Q_UNTILT = K_Q_MPU_FAST;
        untilt_smooth = true;  // MPU6050 is best if smoothed
    }  else {
        Serial.println("No untilter accelerometer found. Make sure the telescope mount is perfectly level");
        return;
    }
    kf_untilt_x = new SimpleKalmanFilter(K_ERR_UNTILT, K_ERR_UNTILT, K_Q_UNTILT);
    kf_untilt_y = new SimpleKalmanFilter(K_ERR_UNTILT, K_ERR_UNTILT, K_Q_UNTILT);
    kf_untilt_z = new SimpleKalmanFilter(K_ERR_UNTILT, K_ERR_UNTILT, K_Q_UNTILT);
}

bool sensors() {
    float K_ERR_ACC;
    float K_Q_ACC;
    float K_ERR_MAG;
    float K_Q_MAG;
    Wire.begin();
    // Search for Altitude Accelerometer - supported LSM and MMA
    if(init_accelerometer_LSM()) {
        Serial.println("LSM6DSV16X Accel/Gyro found");
        LSM_ACCEL = true;
        ACCEL_DATARATE = ACCEL_DATARATE_LSM;
        K_ERR_ACC = K_ERR_A_LSM6;
        K_Q_ACC = K_Q_A_LSM6;
        acc_smooth = false;  // LSM6DSV does not require smoothing
    } else if(init_accelerometer_MMA()) {
        MMA_ACCEL = true;
        ACCEL_DATARATE = ACCEL_DATARATE_MMA;
        K_ERR_ACC = K_ERR_MMA;
        K_Q_ACC = K_Q_MMA;
        acc_smooth = true;  // MMA8451 is best if smoothed
        Serial.println("MMA8451 Accelerometer Found");
    }  else {
        Serial.println("Error, accelerometer not found");
        return false;
    }
    kf_acc_x = new SimpleKalmanFilter(K_ERR_ACC, K_ERR_ACC, K_Q_ACC);
    kf_acc_y = new SimpleKalmanFilter(K_ERR_ACC, K_ERR_ACC, K_Q_ACC);
    kf_acc_z = new SimpleKalmanFilter(K_ERR_ACC, K_ERR_ACC, K_Q_ACC);


    if(init_magnetometer_LIS3MDL()) {
        Serial.println("LIS3MDL Magnetometer Found");
        LIS3MDL_MAG = true;
        MAG_DATARATE = MAGNET_DATARATE_LIS3MDL;
        K_ERR_MAG = K_ERR_M_LIS;
        K_Q_MAG = K_Q_M_LIS;
        mag_smooth = true;  // LIS3MDL is best if smoothed
//        mag_smooth = false;  // LIS3MDL is best if smoothed
        findUntilter();
    } else if(init_magnetometer_R3100()) {
        Serial.println("RM3100 Magnetometer Found");
        RM3100_MAG = true;
        MAG_DATARATE = dataRate_RM3100();
        K_ERR_MAG = K_ERR_M_RM3100;
        K_Q_MAG = K_Q_M_RM3100;
        mag_smooth = true;
        findUntilter();
    } else {
        Serial.println("Error, magnetometer not found");
        return false;
    }
    kf_mag_x = new SimpleKalmanFilter(K_ERR_MAG, K_ERR_MAG, K_Q_MAG);
    kf_mag_y = new SimpleKalmanFilter(K_ERR_MAG, K_ERR_MAG, K_Q_MAG);
    kf_mag_z = new SimpleKalmanFilter(K_ERR_MAG, K_ERR_MAG, K_Q_MAG);
    return true;
}

void rotate(float raw[3], bool force=false) {
  if(sensor_block_vertical | force) {
    float x = raw[0];
    float y = raw[2];
    float z = -raw[1];
    raw[0] = x;
    raw[1] = y;
    raw[2] = z;
  }
}

void mag_readings(float mag_raw[3], uint8_t debug) {
  if(LIS3MDL_MAG){
    mag_readings_LIS(mag_raw);
  } else if(RM3100_MAG) {
    mag_readings_RM3100(mag_raw);
  }
  rotate(mag_raw);
  if(mag_smooth) {
      mag_raw[0] = kf_mag_x->updateEstimate(mag_raw[0]);
      mag_raw[1] = kf_mag_y->updateEstimate(mag_raw[1]);
      mag_raw[2] = kf_mag_z->updateEstimate(mag_raw[2]);
  }
  mag_raw[0] /= B;  // non ho ancora tolto HI/SI ma va bene lo stesso
  mag_raw[1] /= B;  // perchè sto solo riscalando, non normalizzando
  mag_raw[2] /= B;
  if((uint8_t)(debug | ~DEBUG_MAG_RAW)==255) {
      Serial.print("MAG ");Serial.print(mag_raw[0], 4);Serial.print(" ");Serial.print(mag_raw[1], 4);Serial.print(" ");Serial.println(mag_raw[2], 4);
  }
}

void accel_readings(float accel_raw[3], uint8_t debug, bool smooth=true) {
  if(LSM_ACCEL){
    accel_readings_LSM(accel_raw);
  } else if(MMA_ACCEL) {
    accel_readings_MMA(accel_raw);
  }
  rotate(accel_raw, true);
  if(acc_smooth) {
      accel_raw[0] = kf_acc_x->updateEstimate(accel_raw[0]);
      accel_raw[1] = kf_acc_y->updateEstimate(accel_raw[1]);
      accel_raw[2] = kf_acc_z->updateEstimate(accel_raw[2]);
  }

  if((uint8_t)(debug | ~DEBUG_ALT_ACC)==255) {
    Serial.print("ACC ");Serial.print(accel_raw[0]);Serial.print(" ");Serial.print(accel_raw[1]);Serial.print(" ");Serial.println(accel_raw[2]);
  }
}
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

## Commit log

2023-01-12 arduino commit
2023-01-12 arduino readme
2023-01-13 hardware schematics
    [goto-exp-B_Cu.gbr, goto-exp-B_Mask.gbr, goto-exp-B_SilkS.gbr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]
2023-06-20 debouncing juystick button
2023-06-24 accel calibration
2023-06-26 adjusted compass kalman filter
2023-10-14 - refactored sensors management - added magnetometer compensation
2024-04-11 gazer firmware v 0.5
    [config.txt]
2024-06-11 split sketch in 2D and 3D calibration
